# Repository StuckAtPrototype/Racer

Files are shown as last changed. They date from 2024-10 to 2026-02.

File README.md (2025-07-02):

# Micro Racer Car - StuckAtPrototype

*thank you for the overwhelmingly positve support!! such an inspiration to keep making fun open source content!*

## New Youtube video about improvements 
Lots of new improvements and I am now selling a kit for these! Check out the video here:
https://www.youtube.com/watch?v=FulhEs5R5WU
My Kickstarter failed, so I open sourced it (https://www.youtube.com/watch?v=FulhEs5R5WU)

## Original Youtube Video
A bit of a back-story of how this project came to be. 

My Kickstarter failed, so I open sourced it (https://www.youtube.com/watch?v=6jzG-BMannc)

Sub if you like what you see.

*Some pictures of the project*

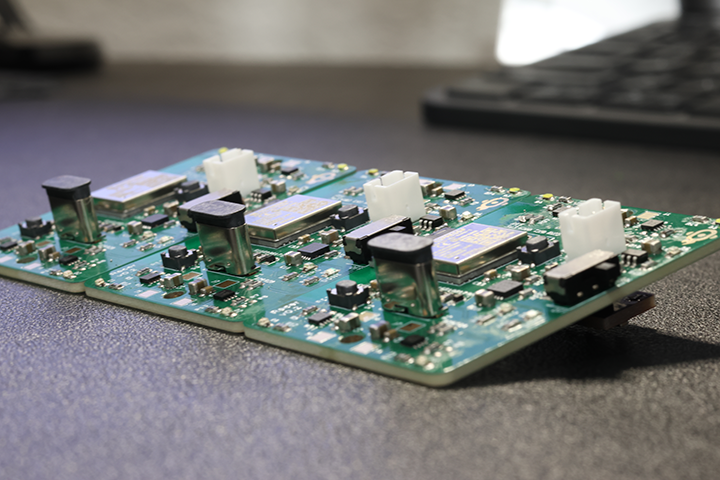
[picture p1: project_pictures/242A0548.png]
Picture of PCB car


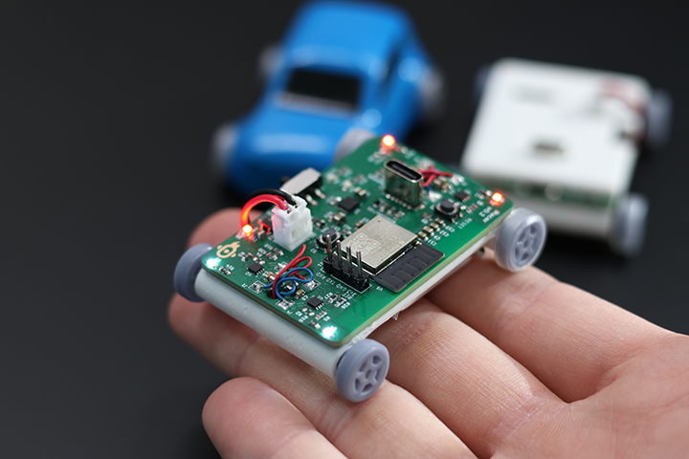
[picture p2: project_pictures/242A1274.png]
Picture of PCB car


## Hardware Remote for this car

https://github.com/StuckAtPrototype/Thumbtroller

## Project Structure
The project consists of
1. Firmware
2. Hardware
3. Mechanical 
4. Scripts

These are structured into their own files. I could have used submodules, but decided against it.  

### 1. Firmware
Code for the little car. This lives on the ESP32

#### Requirements
- ESP32 IDF version 5.3.1
- USB to Serial dongle
- Target set to ESP32-H2

### 2. Hardware

#### Schematic
PDF schematic included for your viewing pleasure. 
#### PCBs
All the gerber files you'd need to send to a fab house. 
#### Kicad
All the files you'd need to expand and work on this further. If you'd like. 

### 3. Mechanical

#### Enclosure
All the step files you need to make one of these. Extrusion printer works well for this part.  

#### Wheels
A bit of caution on this one.. you'll need an SLA printer. 

### 4. Scripts
Did anyone say neural networks? 

This folder has all the python code you'd need to train up your own neural network for the car. It also consists scripts that let you drive it using a keyboard -- just in case you dont want to make a physical controller.  

#### Requirements
- Python 3
- You'll need to install a bunch of pip modules 

#### Training the neural network
Training the neural network is as simple as running the training script with the data in the `color_data.txt` file. For data format see the sample data in the file. You need to stick to the formatting. 

To train run `python trainer.py`

#### Keyboard controller
To run the script `python controller.py`

Use `w` `s` `a` `d` for control. Modify the script for different speeds, etc

*Protocol for motor control* 

60,1,60,1,5 -- translates to:

motor side A: speed 60, direction forward

motor side B: speed 60, direction forward

500 miliseconds run time

See firmware file `motor.c` if you need more details

## What the project could use
1. Cleanup, but thats true for almost anything out there
2. Some fun code that makes the little car drive using the color sensor -- think very fancy line follower
3. LLM integration -- ChatGPT driving a physical little robot? anyone? :)

## If you take it further
Let me know if you ever make one of these, I'd love to see it. Seriously, that'd be exciting and inspiring to keep making my projects open source!

---
## License
### Apache 2.0 -- i.e. use as you'd like
http://www.apache.org/licenses/LICENSE-2.0

--- 
## Special Thanks
Thanks to Michael Angerer for his open sourced `esp32_ble_ota` project. I used it to get BLE running in this project. His blog post and github repo are a great resource. Check it out. https://github.com/michael-angerer/esp32_ble_ota

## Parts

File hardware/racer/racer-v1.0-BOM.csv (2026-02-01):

Designator | Quantity | Manufacturer Part Number | Package/Footprint | Description
U9 | 1 | TPS631000DRLR | TPS631000DRLR_TEX | TPS631000DRLR
R6,R26,R28,R29,R9,R1,R27,R11,R4 | 9 | WR06X103 JTL | R_0603_1608Metric | 10K
C2,C16,C20,C18,C5,C6,C19,C1,C22 | 9 | GRM188R61A106ME69D | C_0603_1608Metric | 10uF
S2 | 1 | RKB2SJK250SMTR LFS | SWITCH_0SMTRLFS | SWITCH_0SMTRLFS
C7,C12,C13,C24,C15,C3,C8,C14,C4,C23,C11,C25 | 12 | CC0603KRX7R7BB104 | C_0603_1608Metric | 0.1uF
R2 | 1 | RQ73C1J806RBTDF | R_0603_1608Metric | 806
U6 | 1 | AP2205-33W5-7 | AP2204 | AP2205
R23 | 1 | RT0603BRE071K43L | R_0603_1608Metric | 1.43K
J9 | 1 | GRPB032VWQS-RC | PinHeader_2x03_P1.27mm_Vertical_SMD | Conn_02x03_SMT
Q1 | 1 | BSS138 | SOT-23 | BSS138
D9 | 1 | 150060RS75000 | C_0603_1608Metric | LED_RED
R17,R22,R18 | 3 | RC0603FR-075K1L | R_0603_1608Metric | 5K1
LED1,LED3,LED5,LED4,LED2 | 5 | IN-PI15TAT5R5G5B | IN-PI15_INL | IN-PI15TAT5R5G5B
D8 | 1 | 150060GS75000 | C_0603_1608Metric | LED_GREEN
U4,U1,U2,U3 | 4 | A3908EEETR-T | A3908 | A3908
J12 | 1 | B2B-PH-K-S | JST_PH_B2B-PH-K_1x02_P2.00mm_Vertical | JST 2.0 BATT
P1 | 1 | USB4105-GF-A | GCT_USB4105-GF-A | USB_C_Plug_USB2.0
TH1 | 1 | NTCG163JF103HT1 | R_0603_1608Metric | TH 10K
U5 | 1 | ESP32-H2-MINI-1 | MODULE_ESP32-H2-MINI-1-H2 | ESP32-H2-MINI-1
R3 | 1 | CR0603-FX-91R0ELF | R_0603_1608Metric | 91
R5 | 1 | ESR03EZPF4700 | R_0603_1608Metric | 470
L1 | 1 | CIGT252010EH1R0MNE | RES_CIGT252010 | 1uH
C10 | 1 | CC0603KRX5R8BB105 | C_0603_1608Metric | 1uF
R21,R20 | 2 | RC0603JR-07330RL | R_0603_1608Metric | 330
D5 | 1 | TPD1E10B06DYAR | D_SOD-523 | TPD1E10B06
S1 | 1 | JS102011SAQN | SW_JS102011SAQN | JS102011SAQN
R24 | 1 | ERJ-PB3B7502V | R_0603_1608Metric | 75K
U7 | 1 | MCP73833T-AMI/MF | SON50P300X300X100-11N | MCP73833
C17 | 1 | GRM188R60J226MEA0J | C_0603_1608Metric | 22uF
R16 | 1 | RMCF0603FT1M00 | R_0603_1608Metric | 1M
C9 | 1 | GRM188C80E476ME05D | C_0603_1608Metric | 47uF
C21 | 1 | CL10A225KO8NNNC | C_0603_1608Metric | 2.2uF

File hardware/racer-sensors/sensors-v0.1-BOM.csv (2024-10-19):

Id | Designator | Footprint | Quantity | Designation | Supplier and ref | Notes
1 | R4,R5,R6,R3 | R_0603_1608Metric | 4 | 10K | WR06X103 JTL
2 | D1,D2 | LED_0603_1608Metric | 2 | LED | IN-S63AT5UW
3 | R2,R1 | R_0603_1608Metric | 2 | R | ESR03EZPF4700 | Note: I used a 470ohm resistor, but this might need to be adjusted to vary brightness
4 | C3 | C_0603_1608Metric | 1 | 4.7uF | GRM188R61A106ME69D | Replaced with 10uF
5 | C1,C2 | C_0603_1608Metric | 2 | 0.1uF | CC0603KRX7R7BB104
6 | U2 | SOT-23_TO-236_TDK | 1 | HAL1501SU-A | HAL1501SU-A
7 | U1 | FCSOT8_DTS_TEX | 1 | OPT4060DTSR | OPT4060DTSR
8 | J1 | PinHeader_2x03_P1.27mm_Vertical_SMD | 1 | Conn_02x03_SMT | 20021321-00006C4LF

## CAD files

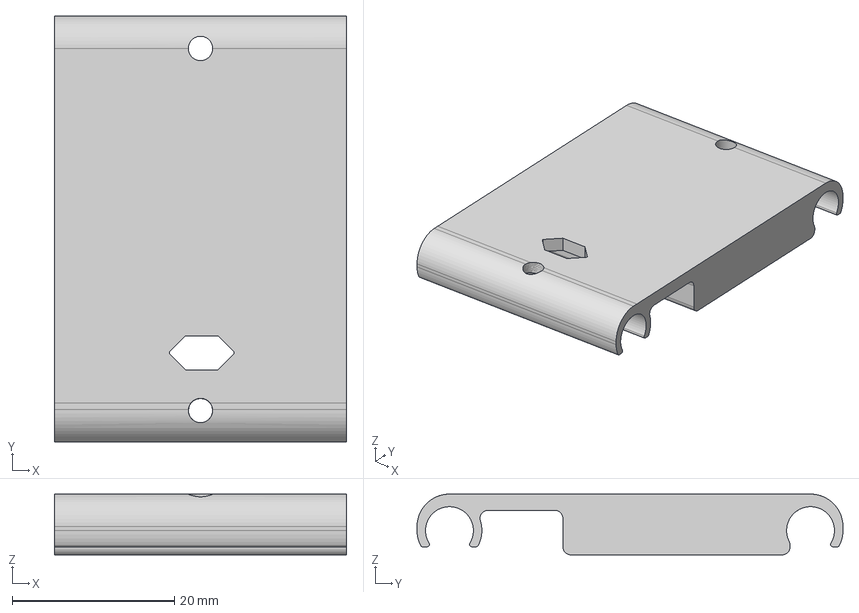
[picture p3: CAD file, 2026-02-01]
mechanical/main-enclosure-v1.0.step
36.0 x 52.5 x 7.50 mm

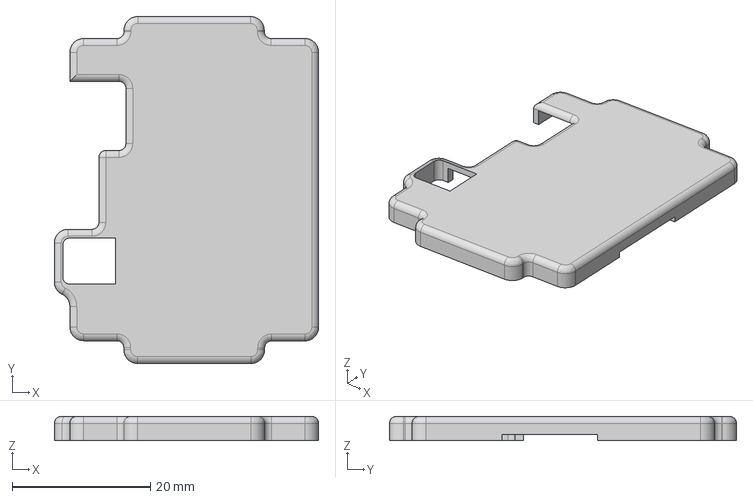
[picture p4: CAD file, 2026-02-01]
mechanical/top-enclosure-v1.0.step
38.2 x 50.2 x 3.50 mm

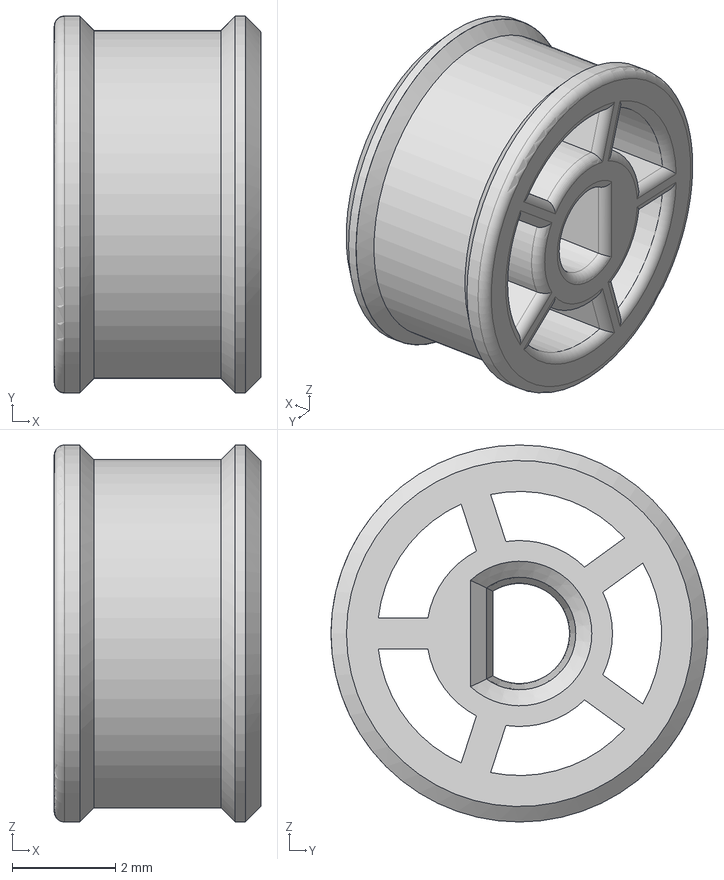
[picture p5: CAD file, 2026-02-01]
mechanical/wheel-v1.0.step
4.00 x 7.30 x 7.30 mm

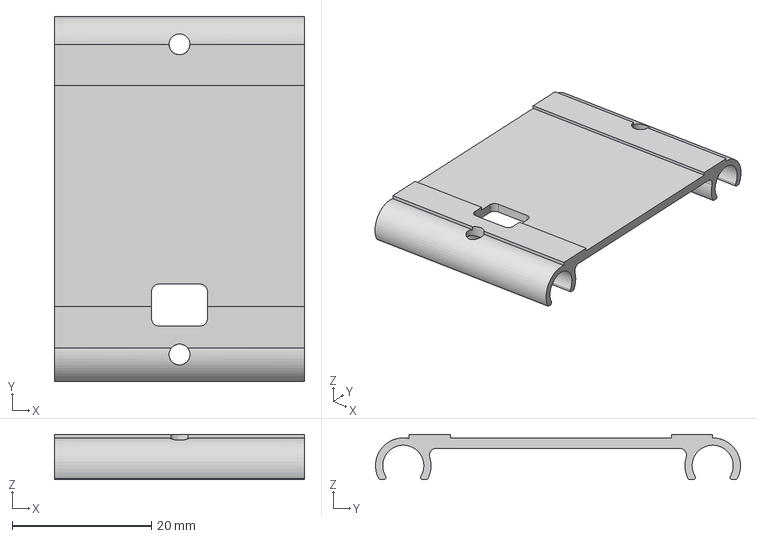
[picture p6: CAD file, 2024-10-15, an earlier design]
mechanical/previous versions/main-enclosure.step
36.0 x 52.5 x 6.50 mm

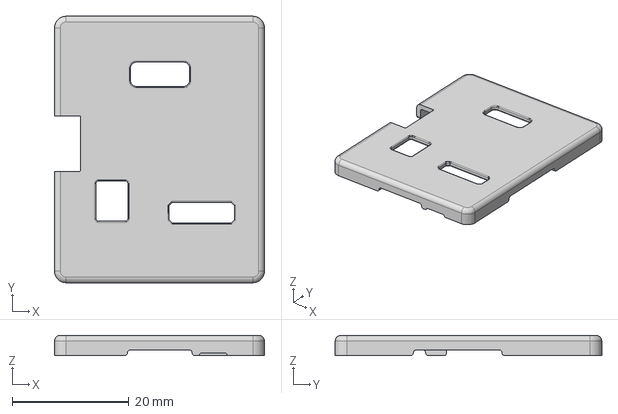
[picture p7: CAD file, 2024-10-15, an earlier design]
mechanical/previous versions/top-enclosure.step
36.0 x 45.7 x 3.50 mm

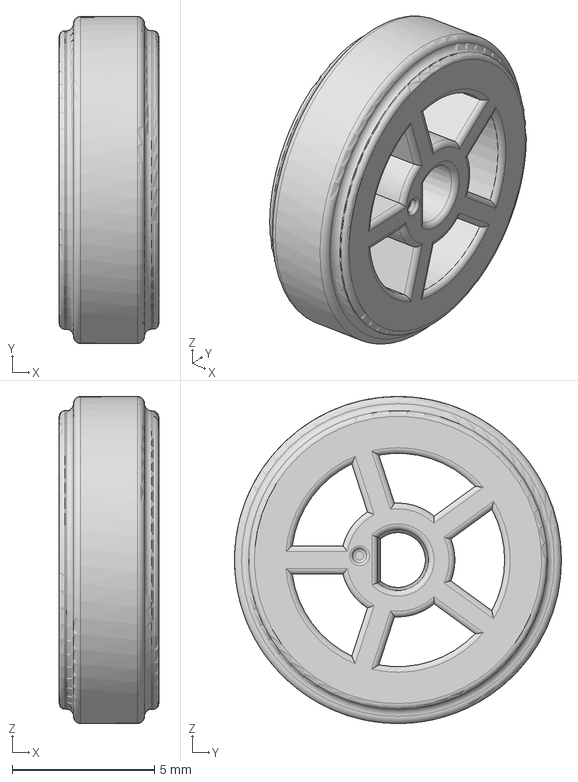
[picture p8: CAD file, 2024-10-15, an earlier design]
mechanical/previous versions/wheel.step
3.50 x 11.5 x 11.5 mm

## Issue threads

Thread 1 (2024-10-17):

PLZ Add PDF for Schematic and PCB artwork

puviarasud, 2024-10-17:
Hi good project. Please add a PDF copy of the schematic and PCB artwork for people to have a look at your design. not all have the tools installed . Thanks

oscarpeters, 2024-10-17:
Been working on improving readability of the schematics.
[RACER-v0.2.1.pdf](https://github.com/user-attachments/files/17410684/RACER-v0.2.1.pdf)

puviarasud, 2024-10-18:
Thanks , put it in the respective Github folder. I will look into it and suggest improvements, All the best.

StuckAtPrototype, 2024-10-19:
> Been working on improving readability of the schematics. [RACER-v0.2.1.pdf](https://github.com/user-attachments/files/17410684/RACER-v0.2.1.pdf)

if you want to open up a pull request I am happy to merge it in :)

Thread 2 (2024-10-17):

More obvious link to a video

gbraad, 2024-10-17:
Make the image in the `README.md` a screenshot with a play button. That makes it more obvious this is a link to the YouTube video. People do not read headings ;-)

StuckAtPrototype, 2024-10-18:
awesome! thank you! this is a brilliant idea! Ill do that

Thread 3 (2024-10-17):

Suggestion:  Add FPV capability via using esp32 cam.

villimikko, 2024-10-17:
Great project! Look really fun!

I think possibly adding FPV would make it perfect ( not sure if controller range is a limit)
Here is example project that is showing it is possible.

https://github.com/RomanLut/hx-esp32-cam-fpv

StuckAtPrototype, 2024-10-18:
neat! this would be fun for sure. I fly FPV freestyle quads and love FPV in general. I might make some youtube shorts showcasing the car with a chepo tiny whoop camera on it :)

AirborneEagle, 2024-10-18:
I would certainly be there for that!
To I used to be quite deep into the fpv drone racing world.
I've also built custom fpv RC cars for a small business that I started once.
Thank you for sharing this awesome project!

StuckAtPrototype, 2024-10-19:
I have analog FPV cameras, I used to be deep into freestyle FPV. I even designed my own frames! I still love my frame more than any other out there, sadly not much time to fly these days. I might do a completely from scratch hardware and firmware as a project one day. I know there is a ton of open source stuff, but I have some fun twists in mind :)

That said, I might do a short running around the house with an FPV camera on one of these!

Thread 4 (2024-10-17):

Please add BOMs

alexspurling, 2024-10-17:
It would be helpful to include BOM files for the PCB (including the motors) so we know which parts to order (same goes for the controller project).

tobiasoort, 2024-10-17:
(this way more novice users can use a service like JLCPCB to order the completed PCB and get going quickly too)

Rubines, 2024-10-17:
Thank you for sharing this fun project!
Please add the motor data, do you have a link where I could source them ?

mianzhi, 2024-10-17:
> Thank you for sharing this fun project! Please add the motor data, do you have a link where I could source them ?

I guess they are "6 mm geared coreless motor, 1200 rpm nominal speed at 3V". @StuckAtPrototype thanks for sharing the project, please correct me if i was wrong.

StuckAtPrototype, 2024-10-17:
@mianzhi thats correct!

I will be sharing a BOM late tonight!

for now, you can find the motors by searching "6mm planetary motors 1200 rpm"

Rubines, 2024-10-17:
Thank you both for your help!
@mianzhi @StuckAtPrototype

StuckAtPrototype, 2024-10-18:
initial BOM added for the racer. I still have the sensor board and the controller to do, but that will have to wait until tomorrow 👍

hazerty565, 2024-10-18:
hi, I would like to know whats is motor it is use? have you got a reference? Thank you

StuckAtPrototype, 2024-10-19:
All BOMs are in! if there are any problems, lets open a new issue. closing this out 🎉

Closed 2024-10-19.

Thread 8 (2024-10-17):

Use USB Pins for programming

majuss, 2024-10-17:
Hi there,

thank you for sharing your project!  The H2-mini is a "C6 variant" which means it comes with onboard USB, no programmer etc. neccessary! Why didn't you connect the D- and D+ lines of the USB-C port to the MCU. That way you could easily program it via USB and could skip the UART header entirely.

StuckAtPrototype, 2024-10-19:
Hi! thats so true! I will do that for the next project. Thanks!! For this project, I would have to upgrade the connector as the one I used does only power. But this is a very good idea. Ill keep it in mind for the project I am working on now :) Closing this out for this one. thanks again!

andistorm, 2024-11-06:
Nice idea,

currently there is only a 6-pin USB-C connector used. If i am not wrong, you would need at least 8 pins, with `D-` and `D+`.

This would mean we need to change pcb, which we try not to do for `v0.2.0` release, but after checking at JLCPCB I realized this connector is currently not available, so maybe we need to change USB-C Connector anyways.

Since this issue is in discussion again, I reopen it.

What do you think @StuckAtPrototype

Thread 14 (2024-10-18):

CPL file

AirborneEagle, 2024-10-18:
I am totally new to the world of PCB making and assembly.
Do you have a cpl file that you could include?

StuckAtPrototype, 2024-10-18:
ill add it to the list, thats a good point!

TexGG, 2024-10-19:
I was gonna ask the same. The project look amasing, the CPL will hepl produce the circuit easier :)

mr-ukas, 2024-10-30:
I created a pick&place file from Kicad. First time in my life, so better double check : D
For getting a PCBA-manufacturer's quote, it should be good enough 👍

PCB top edited to match JLCPCB requirements to format.
[racer-top-pos.csv](https://github.com/user-attachments/files/17579037/racer-top-pos.csv)
[CPL_miniRacer_position_pickNplace_JLC_top.xlsx](https://github.com/user-attachments/files/17579038/CPL_miniRacer_position_pickNplace_JLC_top.xlsx)
[racer-bottom-pos.csv](https://github.com/user-attachments/files/17579039/racer-bottom-pos.csv)

mr-ukas, 2024-10-30:
all revision V0.2

mr-ukas, 2024-10-30:
`What do you mean by this? Is it not based on master branch?`
It's the master branch. I just wanted to add this information about the revision, in case somebody will update the revision in the future.

`where you explain the steps you have done 👀`

I just re-named the columns according to this guide here:
https://jlcpcb.com/help/article/pick-place-file-for-pcb-assembly

andistorm, 2024-10-30:
>I just re-named the columns according to this guide here

Oh wow, you typed in all the rows by hand? I would have thought there is some tooling to  achieve this.

Did you have a look at [this guide](https://jlcpcb.com/help/article/How-to-generate-the-BOM-and-Centroid-file-from-KiCAD)?

mr-ukas, 2024-10-30:
> Did you have a look at [this guide](https://jlcpcb.com/help/article/How-to-generate-the-BOM-and-Centroid-file-from-KiCAD)?

yes, true, this page was my starting point.
I used also the MS excel to import the CSV-file to a regular excel sheet. This transferred the rows to proper columns, which had to be re-named ✌️

mr-ukas, 2024-10-30:
Feel free to creat a pull request to merge the files. I have no idea how this is done. It's late here :D

andistorm, 2024-10-30:
> Feel free to creat a pull request to merge the files.

Probably I will, but I want to try to generate this files by myself for this

fschrempf, 2024-11-07:
I'm usually using [Aisler](https://aisler.net/) to order PCBs (and optionally parts/assembly). They allow to upload the KiCad PCB file and get all the required data from it. For matching the components automatically it requires a ["MPN" field](https://community.aisler.net/t/documenting-parts/56) to be set as the "Manufacturer Part Number". I don't know the requirements for JLCPCB, but it would be great if we could also add the MPN field.

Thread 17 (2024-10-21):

Circuit boards

smebberson, 2024-10-21:
Are there only services that will allow me to have one the PCB printed with all of the electrical components in place? Are all of the files available for this project that would be needed for such a service?

I have no idea about how to make the final circuit board with everything soldered in place, but I would like to try and build this project.

I'm a software guy with some ESP32 programming experience

StuckAtPrototype, 2024-10-21:
Everything necessary is within the repo, that said, I will generate placement files which will make it much easier. I am happy that you want to build it! I would love to see it once you are done :) Also, feel free to open a thread in the discussions if you need any help! thanks for the support

Closed 2024-10-21.

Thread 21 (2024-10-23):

request for the charging circuit design and details used in the project

nithinmathewjoji, 2024-10-23:
# Request for LiPo Charger Circuit Design details

Dear **Mr. StuckAtPrototype**,

Kindly provide the circuit schematic, explaining:
   - The connections between components.
   - The placement of safety components like diodes and fuses.
   - Input/output terminals and how they interface with the battery.

blubbsy, 2024-10-23:
Hi,

is there a reason why to use a GPT text for asking this? But to answer your question: For the project simply the Microchip MCP73833 is used and in the datasheet you find this picture with values:

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

nithinmathewjoji, 2024-10-24:
Naa I'm just too lazy to type the whole thing dude 😆 🤣

DeepCoreSystem, 2024-10-24:
Open the KiCad project and you'll find the schematic

StuckAtPrototype, 2024-11-03:
everything needed is in the files. closing this out

Closed 2024-11-03.

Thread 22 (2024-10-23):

Question on Racer outside shell

aushe02, 2024-10-23:
I was looking at the mechanical step files and noticed there isn't a file for the outside shell of the Racer that goes over the enclosure, like in the picture below. I was wondering if you 3D printed that part. If you did, could you upload the file?

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

StuckAtPrototype, 2024-10-25:
The original body does not fit the new version and at this point id have to dig deep to find the original body files. But, yes it was printed on an SLA printer

Closed 2024-10-25.

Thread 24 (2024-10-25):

Bom for thumbtroller is missing

Mk-arc, 2024-10-25:
I couldnt find the bom for the controller. Could you also add it?

FrerichsJacob, 2024-10-29:
It's in the Thumbtroller repository!
https://github.com/StuckAtPrototype/Thumbtroller/tree/master/hardware

StuckAtPrototype, 2024-10-30:
closing this out. its here https://github.com/StuckAtPrototype/Thumbtroller/blob/master/hardware/controller-v0.2-BOM.csv

Closed 2024-10-30.

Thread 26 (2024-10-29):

sdkconfig missing

paolosanchi, 2024-10-29:
Hello, I'm trying to compile and run the firmware on an esp32 wroom devkit, I currently don't have a esp mini 1, but I guess it should be compatible.
I could compile it by changing the default configuration (I basically had to activate the BLE).
The file sdkconfig is missing and I'm afraid I miss some kind of configurations.
The firmware runs but it seems to get stuck.
this is the output:

```
I (31) boot: ESP-IDF v5.3.1 2nd stage bootloader
I (31) boot: compile time Oct 29 2024 05:32:28
I (31) boot: Multicore bootloader
I (35) boot: chip revision: v3.0
I (39) boot.esp32: SPI Speed      : 40MHz
I (44) boot.esp32: SPI Mode       : DIO
I (48) boot.esp32: SPI Flash Size : 2MB
I (53) boot: Enabling RNG early entropy source...
I (58) boot: Partition Table:
I (62) boot: ## Label            Usage          Type ST Offset   Length
I (69) boot:  0 nvs              WiFi data        01 02 00009000 00006000
I (77) boot:  1 phy_init         RF data          01 01 0000f000 00001000
I (84) boot:  2 factory          factory app      00 00 00010000 00100000
I (92) boot: End of partition table
I (96) esp_image: segment 0: paddr=00010020 vaddr=3f400020 size=1a2f8h (107256) map
I (141) esp_image: segment 1: paddr=0002a320 vaddr=3ff80000 size=00004h (     4) load
I (141) esp_image: segment 2: paddr=0002a32c vaddr=3ffbdb60 size=04dech ( 19948) load
I (154) esp_image: segment 3: paddr=0002f120 vaddr=40080000 size=00ef8h (  3832) load
I (157) esp_image: segment 4: paddr=00030020 vaddr=400d0020 size=595c0h (366016) map
I (289) esp_image: segment 5: paddr=000895e8 vaddr=40080ef8 size=18570h ( 99696) load
I (341) boot: Loaded app from partition at offset 0x10000
I (341) boot: Disabling RNG early entropy source...
I (353) cpu_start: Multicore app
I (362) cpu_start: Pro cpu start user code
I (362) cpu_start: cpu freq: 160000000 Hz
I (362) app_init: Application information:
I (365) app_init: Project name:     hello_world
I (370) app_init: App version:      1807a4c-dirty
I (375) app_init: Compile time:     Oct 29 2024 12:30:22
I (381) app_init: ELF file SHA256:  8ac5c9a1f...
I (387) app_init: ESP-IDF:          v5.3.1
I (391) efuse_init: Min chip rev:     v0.0
I (396) efuse_init: Max chip rev:     v3.99
I (401) efuse_init: Chip rev:         v3.0
I (406) heap_init: Initializing. RAM available for dynamic allocation:
I (413) heap_init: At 3FFAFF10 len 000000F0 (0 KiB): DRAM
I (419) heap_init: At 3FFB6388 len 00001C78 (7 KiB): DRAM
I (425) heap_init: At 3FFB9A20 len 00004108 (16 KiB): DRAM
I (431) heap_init: At 3FFC5CC8 len 0001A338 (104 KiB): DRAM
I (438) heap_init: At 3FFE0440 len 00003AE0 (14 KiB): D/IRAM
I (444) heap_init: At 3FFE4350 len 0001BCB0 (111 KiB): D/IRAM
I (450) heap_init: At 40099468 len 00006B98 (26 KiB): IRAM
I (458) spi_flash: detected chip: winbond
I (461) spi_flash: flash io: dio
W (465) spi_flash: Detected size(4096k) larger than the size in the binary image header(2048k). Using the size in the binary image header.
W (479) i2c: This driver is an old driver, please migrate your application code to adapt `driver/i2c_master.h`
I (490) coexist: coex firmware version: 4482466
I (495) main_task: Started on CPU0
I (505) main_task: Calling app_main()
I (505) gpio: GPIO[27]| InputEn: 0| OutputEn: 1| OpenDrain: 0| Pullup: 0| Pulldown: 0| Intr:0
I (505) gpio: GPIO[26]| InputEn: 0| OutputEn: 1| OpenDrain: 0| Pullup: 0| Pulldown: 0| Intr:0
I (515) gpio: GPIO[25]| InputEn: 0| OutputEn: 1| OpenDrain: 0| Pullup: 0| Pulldown: 0| Intr:0
I (525) gpio: GPIO[22]| InputEn: 0| OutputEn: 1| OpenDrain: 0| Pullup: 0| Pulldown: 0| Intr:0
LED flash period set to 10 ticks
LED 0 (GPIO 27) set to ON
LED 1 (GPIO 26) set to ON
LED 2 (GPIO 25) set to ON
LED 3 (GPIO 22) set to ON
LED 3 (GPIO 22) set to OFF
LED 2 (GPIO 25) set to OFF
LED 1 (GPIO 26) set to ON
LED 0 (GPIO 27) set to ON
I (565) BTDM_INIT: BT controller compile version [b022216]
I (565) BTDM_INIT: Bluetooth MAC: 40:22:d8:57:e3:b6
I (575) phy_init: phy_version 4830,54550f7,Jun 20 2024,14:22:08
I (895) gpio: GPIO[10]| InputEn: 1| OutputEn: 0| OpenDrain: 0| Pullup: 1| P
```
As you can see the last line is interrupted

StuckAtPrototype, 2024-10-30:
Hi, Ill add the sdkconfig, thats a good point. I never ran this firmware on anything but the esp32-h2, so not sure it would run. there could be a GPIO collision from what it looks like

paolosanchi, 2024-10-31:
Ok, I wait for the sdkconfig, meanwhile I'll get an esp-h2 devboard and try to build my own car.
I really love this project and I'd like to help in its development.
I've texted you in private in instagram, please check out your message requests.

StuckAtPrototype, 2024-11-03:
sdkconfig added

Closed 2024-11-03.

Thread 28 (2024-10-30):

Missing footprint for USB C Connector

andistorm, 2024-10-30:
## My Setup

kicad 8.0.6

## How To Reproduce

1. Checkout `master`branch
2. Open PCB
3. Update PCB from Schematic

## Error Log

```
Error: P1 pad A4 not found in kicad_reformed_custom_IC:CUI_UJC-VP-3-SMT-TR.
Error: P1 pad B4 not found in kicad_reformed_custom_IC:CUI_UJC-VP-3-SMT-TR.
Error: P1 pad A1 not found in kicad_reformed_custom_IC:CUI_UJC-VP-3-SMT-TR.
Error: P1 pad B1 not found in kicad_reformed_custom_IC:CUI_UJC-VP-3-SMT-TR.
Error: P1 pad A6 not found in kicad_reformed_custom_IC:CUI_UJC-VP-3-SMT-TR.
Error: P1 pad A7 not found in kicad_reformed_custom_IC:CUI_UJC-VP-3-SMT-TR.
```

## Explanation

Opening the schematic file show that `kicad_reformed_custom_IC:CUI_UJC-VP-3-SMT-TR` is used as the footprint.
The library `kicad_reformed_custom_IC` comes not with default kicad installation. I guess it was imported once, after choosing the USB C Connector.
The problem is one could only guess which USB C Connector should be used.

## Open Questions

1. Which USB C connector is used?
2. Should we add a custom footprint library to the project? (including this one)

StuckAtPrototype, 2024-11-03:
Thanks for raising the issue, I will create a separate repo with all my footprints, thats should help in the future as well. Connector is CUI_UJC-VP-3-SMT-TR

StuckAtPrototype, 2024-11-03:
added necessary libraries here https://github.com/StuckAtPrototype/StuckAtPrototypeKiCadLibs/tree/master

closing this out for now, though please let me know if it works after setting them up.

andistorm, 2024-11-06:
Unfortunately, that didn’t solve the problem, but I found out that the symbol and footprint didn’t match

See my PR: https://github.com/StuckAtPrototype/Racer/pull/33

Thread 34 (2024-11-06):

Make project ready for Release v0.2.0

andistorm, 2024-11-06:
Let's work on having a `v0.2.0` release.

The idea of this release is to keep the state of software/hardware as it is right now,
but to enable easier fabrication at for example JLCPCB

This issue sums up what is needed to do before releasing:

Bugfixes:
- [ ] https://github.com/StuckAtPrototype/Racer/issues/28 : To allow opening kicad project out of the box (without warnings)

Enhancements:
- [ ] https://github.com/StuckAtPrototype/Racer/issues/14
- [ ] Add documentation: How to remake

Process:
- [ ] Make test order at JLCPCB

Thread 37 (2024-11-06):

Use cheaper Motor Driver from Texas instruments

andistorm, 2024-11-06:
### Discussed in https://github.com/StuckAtPrototype/Racer/discussions/12

<div type='discussions-op-text'>

<sup>Originally posted by **nledevil** October 17, 2024</sup>
I am starting to add LCSC part numbers to the schematic so I can have jcbpcb create/populate the board. I noticed you are using Allegra A3908 brushed dc motor drivers. Is there a reason for this? A3908's are pretty pricey and a Texas Instruments motor driver would be significantly cheaper. Would there be any drawback to using a cheaper driver to make the overall cost per unit lower?</div>

andistorm, 2024-11-06:
If it is a drop-in-replacement we could think about adding this to [`v0.2.0` release](https://github.com/StuckAtPrototype/Racer/issues/34)

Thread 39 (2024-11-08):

Incorrect resistor part number in BOM

FrerichsJacob, 2024-11-08:
Racer and Thumbtroller BOMs list RMCF0603JT5R10 (5.1 ohm) where they should say RMCF0603JT5K10 (5.1k ohm)

StuckAtPrototype, 2024-11-12:
Agreed, thats a mistake in the part number. The entire BOM should be double checked

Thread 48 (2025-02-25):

Instructions to order parts

hdattada, 2025-02-25:
Hi I am a noob trying to figure out how to source all the parts to assemble this. Unfortunately, the documentation currently seems a bit overwhelming for me. I tried to order the enclosure off an online retailer using the step files. It requires the user to configure the material for each of the part. I am sorry if there are already instructions on how to do this. Could someone please help me out?

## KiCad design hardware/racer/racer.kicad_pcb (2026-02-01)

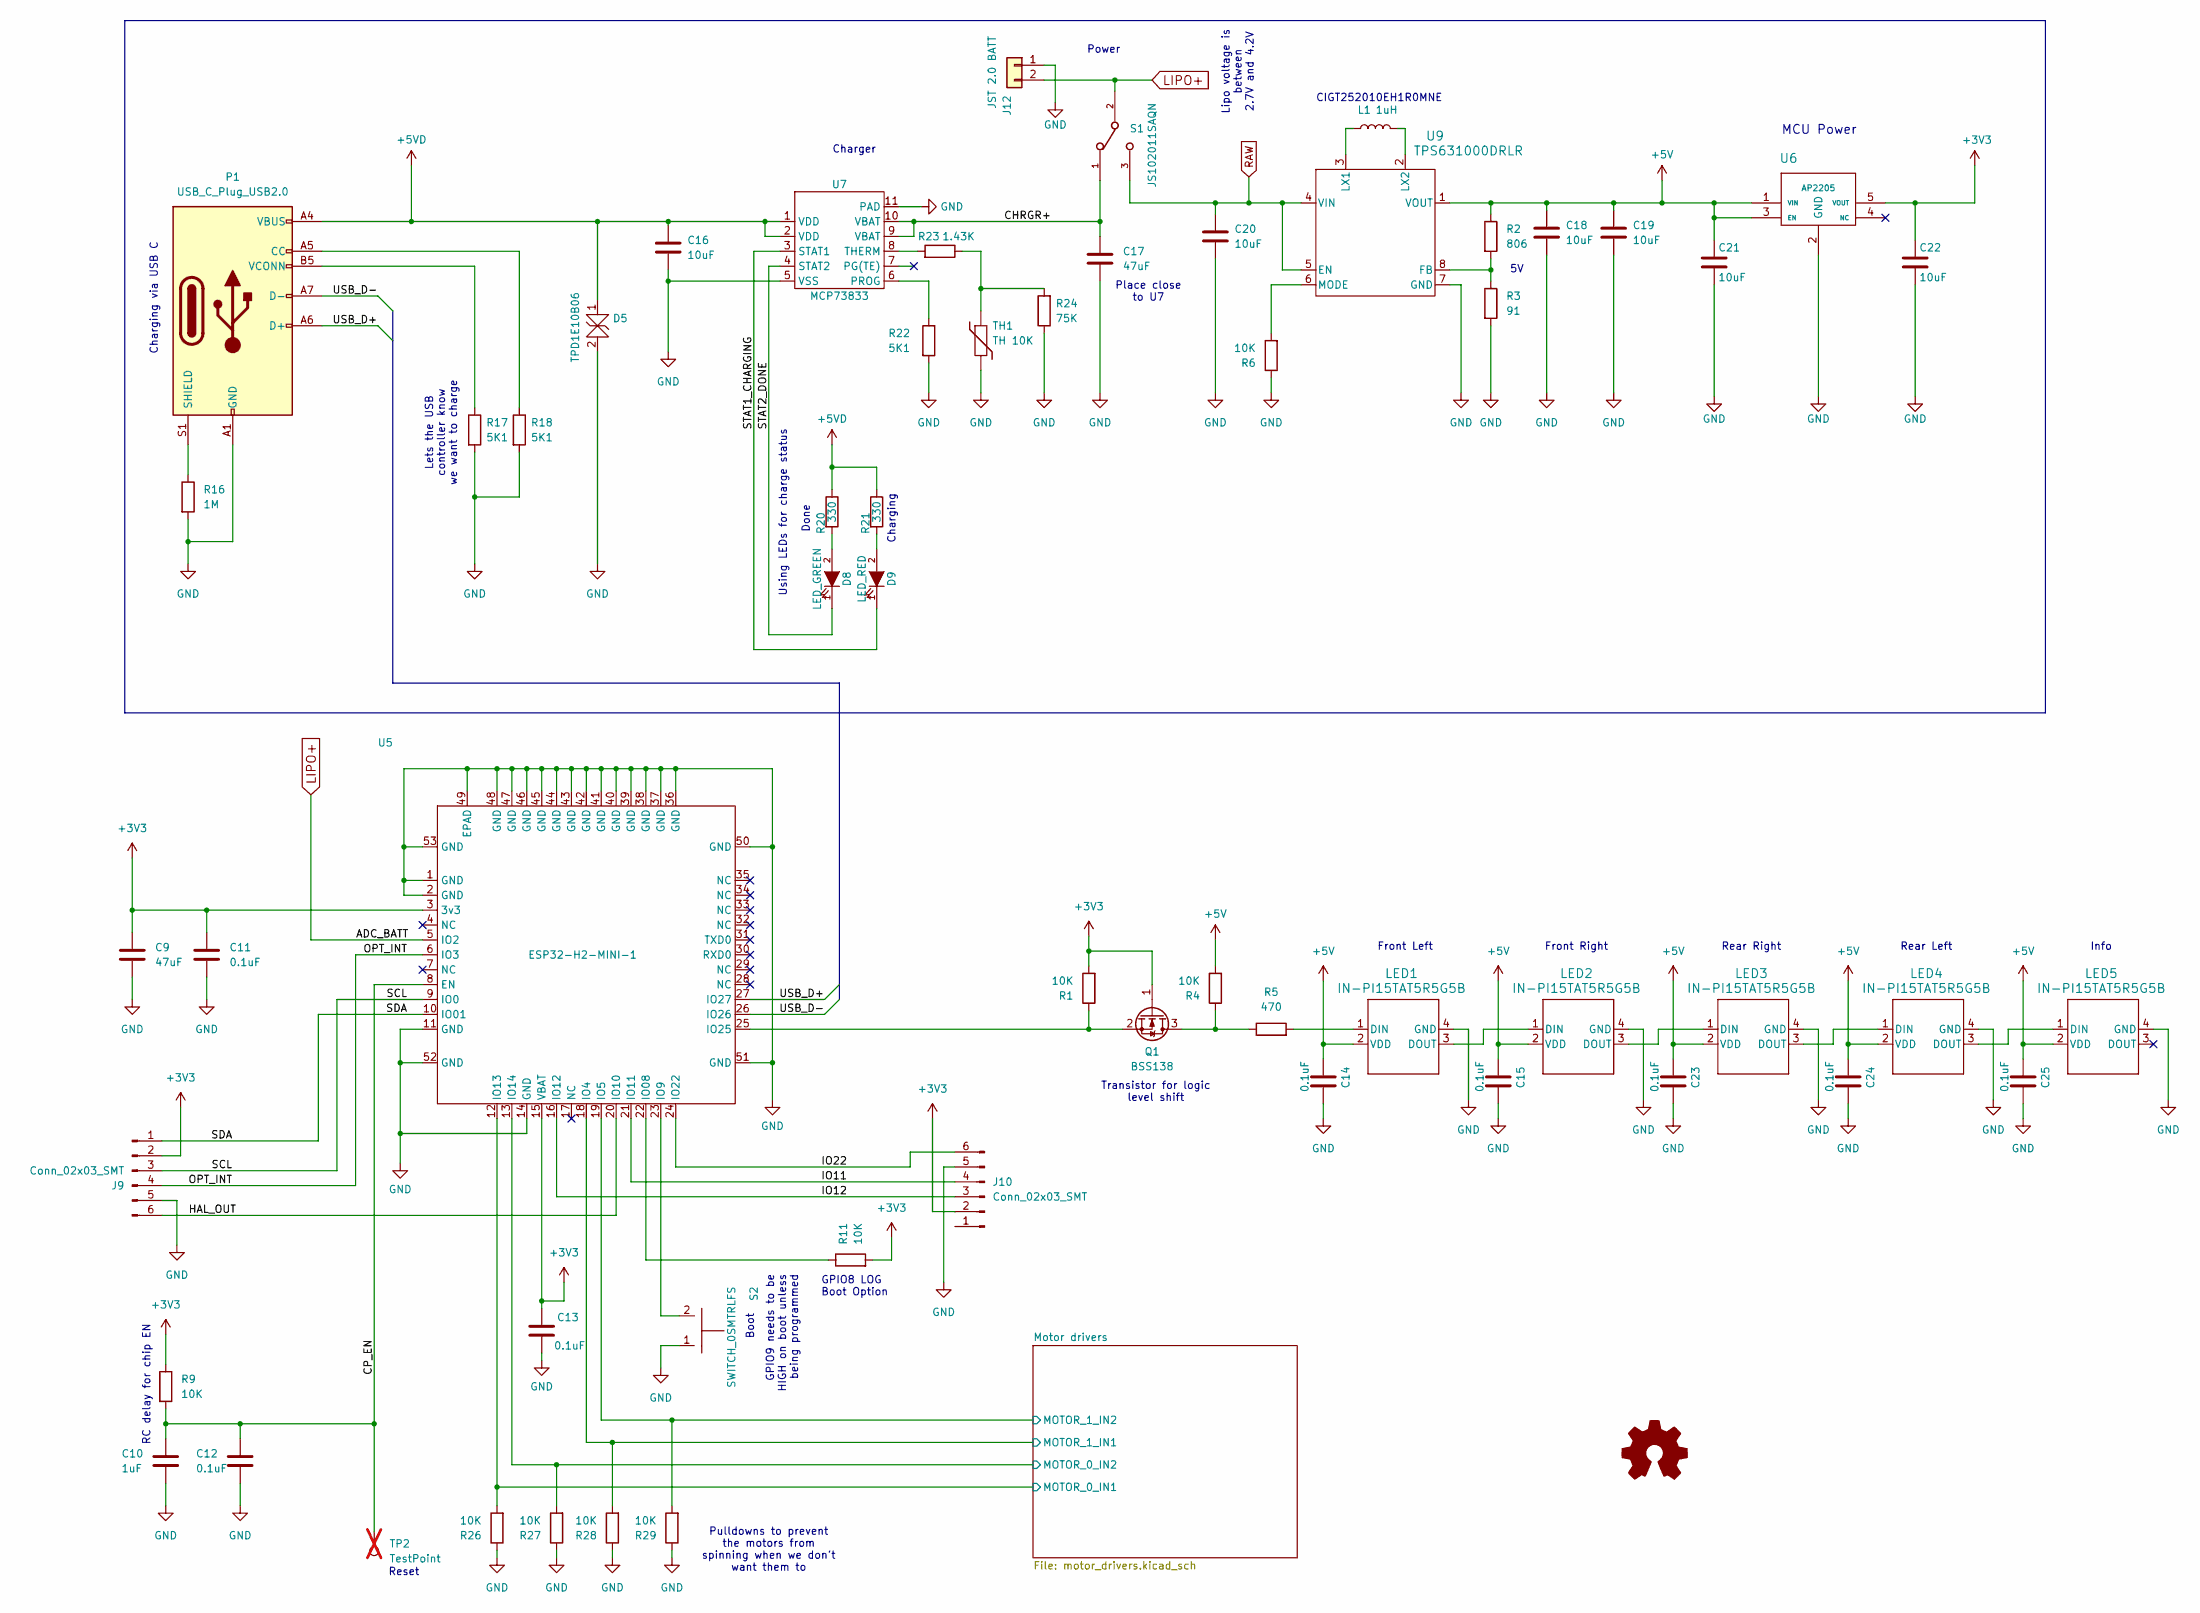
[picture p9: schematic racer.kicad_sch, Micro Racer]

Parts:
C9, C17: 47uF; C_0603_1608Metric
C10: 1uF; C_0603_1608Metric
C11, C12, C13, C14, C15, C23, C24, C25: 0.1uF; C_0603_1608Metric
C16, C18, C19, C20, C21, C22: 10uF; C_0603_1608Metric
D5: TPD1E10B06; D_SOD-523
D8: LED_GREEN; C_0603_1608Metric
D9: LED_RED; C_0603_1608Metric
J9, J10: Conn_02x03_SMT; PinHeader_2x03_P1.27mm_Vertical_SMD
J12: JST 2.0 BATT; JST_PH_B2B-PH-K_1x02_P2.00mm_Vertical
L1: 1uH; RES_CIGT252010
LED1, LED2, LED3, LED4, LED5: IN-PI15TAT5R5G5B; IN-PI15_INL
P1: USB_C_Plug_USB2.0; GCT_USB4105-GF-A
Q1: BSS138; SOT-23
R1, R4, R6, R9, R11, R26, R27, R28, R29: 10K; R_0603_1608Metric
R2: 806; R_0603_1608Metric
R3: 91; R_0603_1608Metric
R5: 470; R_0603_1608Metric
R16: 1M; R_0603_1608Metric
R17, R18, R22: 5K1; R_0603_1608Metric
R20, R21: 330; R_0603_1608Metric
R23: 1.43K; R_0603_1608Metric
R24: 75K; R_0603_1608Metric
S1: JS102011SAQN; SW_JS102011SAQN
S2: SWITCH_0SMTRLFS
TH1: TH 10K; R_0603_1608Metric
TP2: TestPoint; TestPoint_Pad_1.5x1.5mm; not fitted
U5: ESP32-H2-MINI-1; MODULE_ESP32-H2-MINI-1-H2
U6: AP2205; AP2204
U7: MCP73833; SON50P300X300X100-11N
U9: TPS631000DRLR; TPS631000DRLR_TEX

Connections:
+3V3: C9.1, C11.1, C13.1, C22.1, J9.2, J10.2, Q1.1 (G), R1.2, R9.1, R11.2, U5.3 (3v3), U5.15 (VBAT), U6.5 (VOUT)
+5V: C14.1, C15.1, C18.1, C19.1, C21.1, C23.1, C24.1, C25.1, LED1.2 (VDD), LED2.2 (VDD), LED3.2 (VDD), LED4.2 (VDD), LED5.2 (VDD), R2.1, R4.2, U6.1 (VIN), U6.3 (EN), U9.1 (VOUT)
+5VD: C16.1, D5.1, P1.A4 (VBUS), P1.A9 (VBUS), P1.B4 (VBUS), P1.B9 (VBUS), R20.1, R21.1, U7.1 (VDD), U7.2 (VDD)
/CHRGR+: C17.1, S1.1, U7.9 (VBAT), U7.10 (VBAT)
/CP_EN: C10.1, C12.1, R9.2, TP2.1, U5.8 (EN)
/HAL_OUT: J9.6, U5.20 (IO10)
/IO11: J10.4, U5.21 (IO11)
/IO12: J10.3, U5.16 (IO12)
/IO22: J10.6, U5.24 (IO22)
/OPT_INT: J9.4, U5.6 (IO3)
/SCL: J9.3, U5.9 (IO0)
/SDA: J9.1, U5.10 (IO01)
/STAT1_CHARGING: D9.1 (K), U7.3 (STAT1)
/STAT2_DONE: D8.1 (K), U7.4 (STAT2)
/USB_D+: P1.A6 (D+), U5.27 (IO27)
/USB_D-: P1.A7 (D-), U5.26 (IO26)
GND: C9.2, C10.2, C11.2, C12.2, C13.2, C14.2, C15.2, C16.2, C17.2, C18.2, C19.2, C20.2, C21.2, C22.2, C23.2, C24.2, C25.2, D5.2, J9.5, J10.5, J12.1, LED1.4 (GND), LED2.4 (GND), LED3.4 (GND), LED4.4 (GND), LED5.4 (GND), P1.A1 (GND), P1.A12 (GND), P1.B1 (GND), P1.B12 (GND), R3.2, R6.1, R16.2, R17.2, R18.2, R22.2, R24.1, R26.1, R27.1, R28.1, R29.1, S2.1, TH1.2, U5.1 (GND), U5.2 (GND), U5.11 (GND), U5.14 (GND), U5.36 (GND), U5.37 (GND), U5.38 (GND), U5.39 (GND), U5.40 (GND), U5.41 (GND), U5.42 (GND), U5.43 (GND), U5.44 (GND), U5.45 (GND), U5.46 (GND), U5.47 (GND), U5.48 (GND), U5.49 (EPAD), U5.50 (GND), U5.51 (GND), U5.52 (GND), U5.53 (GND), U6.2 (GND), U7.5 (VSS), U7.11 (PAD), U9.7 (GND); also elsewhere on the board
LIPO+: J12.2, S1.2, U5.5 (IO2)
MOTOR_0_IN1: R26.2, U5.12 (IO13); also elsewhere on the board
MOTOR_0_IN2: R27.2, U5.13 (IO14); also elsewhere on the board
MOTOR_1_IN1: R28.2, U5.18 (IO4); also elsewhere on the board
MOTOR_1_IN2: R29.2, U5.19 (IO5); also elsewhere on the board
unnamed: D8.2 (A), R20.2
unnamed: D9.2 (A), R21.2
unnamed: LED1.1 (DIN), R5.2
unnamed: LED1.3 (DOUT), LED2.1 (DIN)
unnamed: LED2.3 (DOUT), LED3.1 (DIN)
unnamed: LED3.3 (DOUT), LED4.1 (DIN)
unnamed: LED4.3 (DOUT), LED5.1 (DIN)
unnamed: P1.A5 (CC), R18.1
unnamed: P1.S1 (SHIELD), R16.1
unnamed: P1.B5 (VCONN), R17.1
unnamed: Q1.3 (D), R4.1, R5.1
unnamed: Q1.2 (S), R1.1, U5.25 (IO25)
unnamed: R23.1, R24.2, TH1.1
unnamed: R11.1, U5.22 (IO08)
unnamed: S2.2, U5.23 (IO9)
unnamed: R22.1, U7.6 (PROG)
unnamed: R23.2, U7.8 (THERM)
unnamed: R2.2, R3.1, U9.8 (FB)
unnamed: L1.1, U9.3 (LX1)
unnamed: L1.2, U9.2 (LX2)
unnamed: R6.2, U9.6 (MODE)
RAW: C20.1, S1.3, U9.4 (VIN), U9.5 (EN); also elsewhere on the board

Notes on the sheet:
Lipo voltage is between 2.7V and 4.2V
Charging via USB C
Using LEDs for charge status
RC delay for chip EN
Lets the USB controller know we want to charge
Front Right
Power
Rear Right
Reset
GPIO9 needs to be HIGH on boot unless being programmed
Pulldowns to prevent the motors from spinning when we don't want them to
Charger
GPIO8 LOG Boot Option
Charging
Done
Info
MCU Power
Front Left
CIGT252010EH1R0MNE
Rear Left
Place close to U7
Boot
Transistor for logic level shift

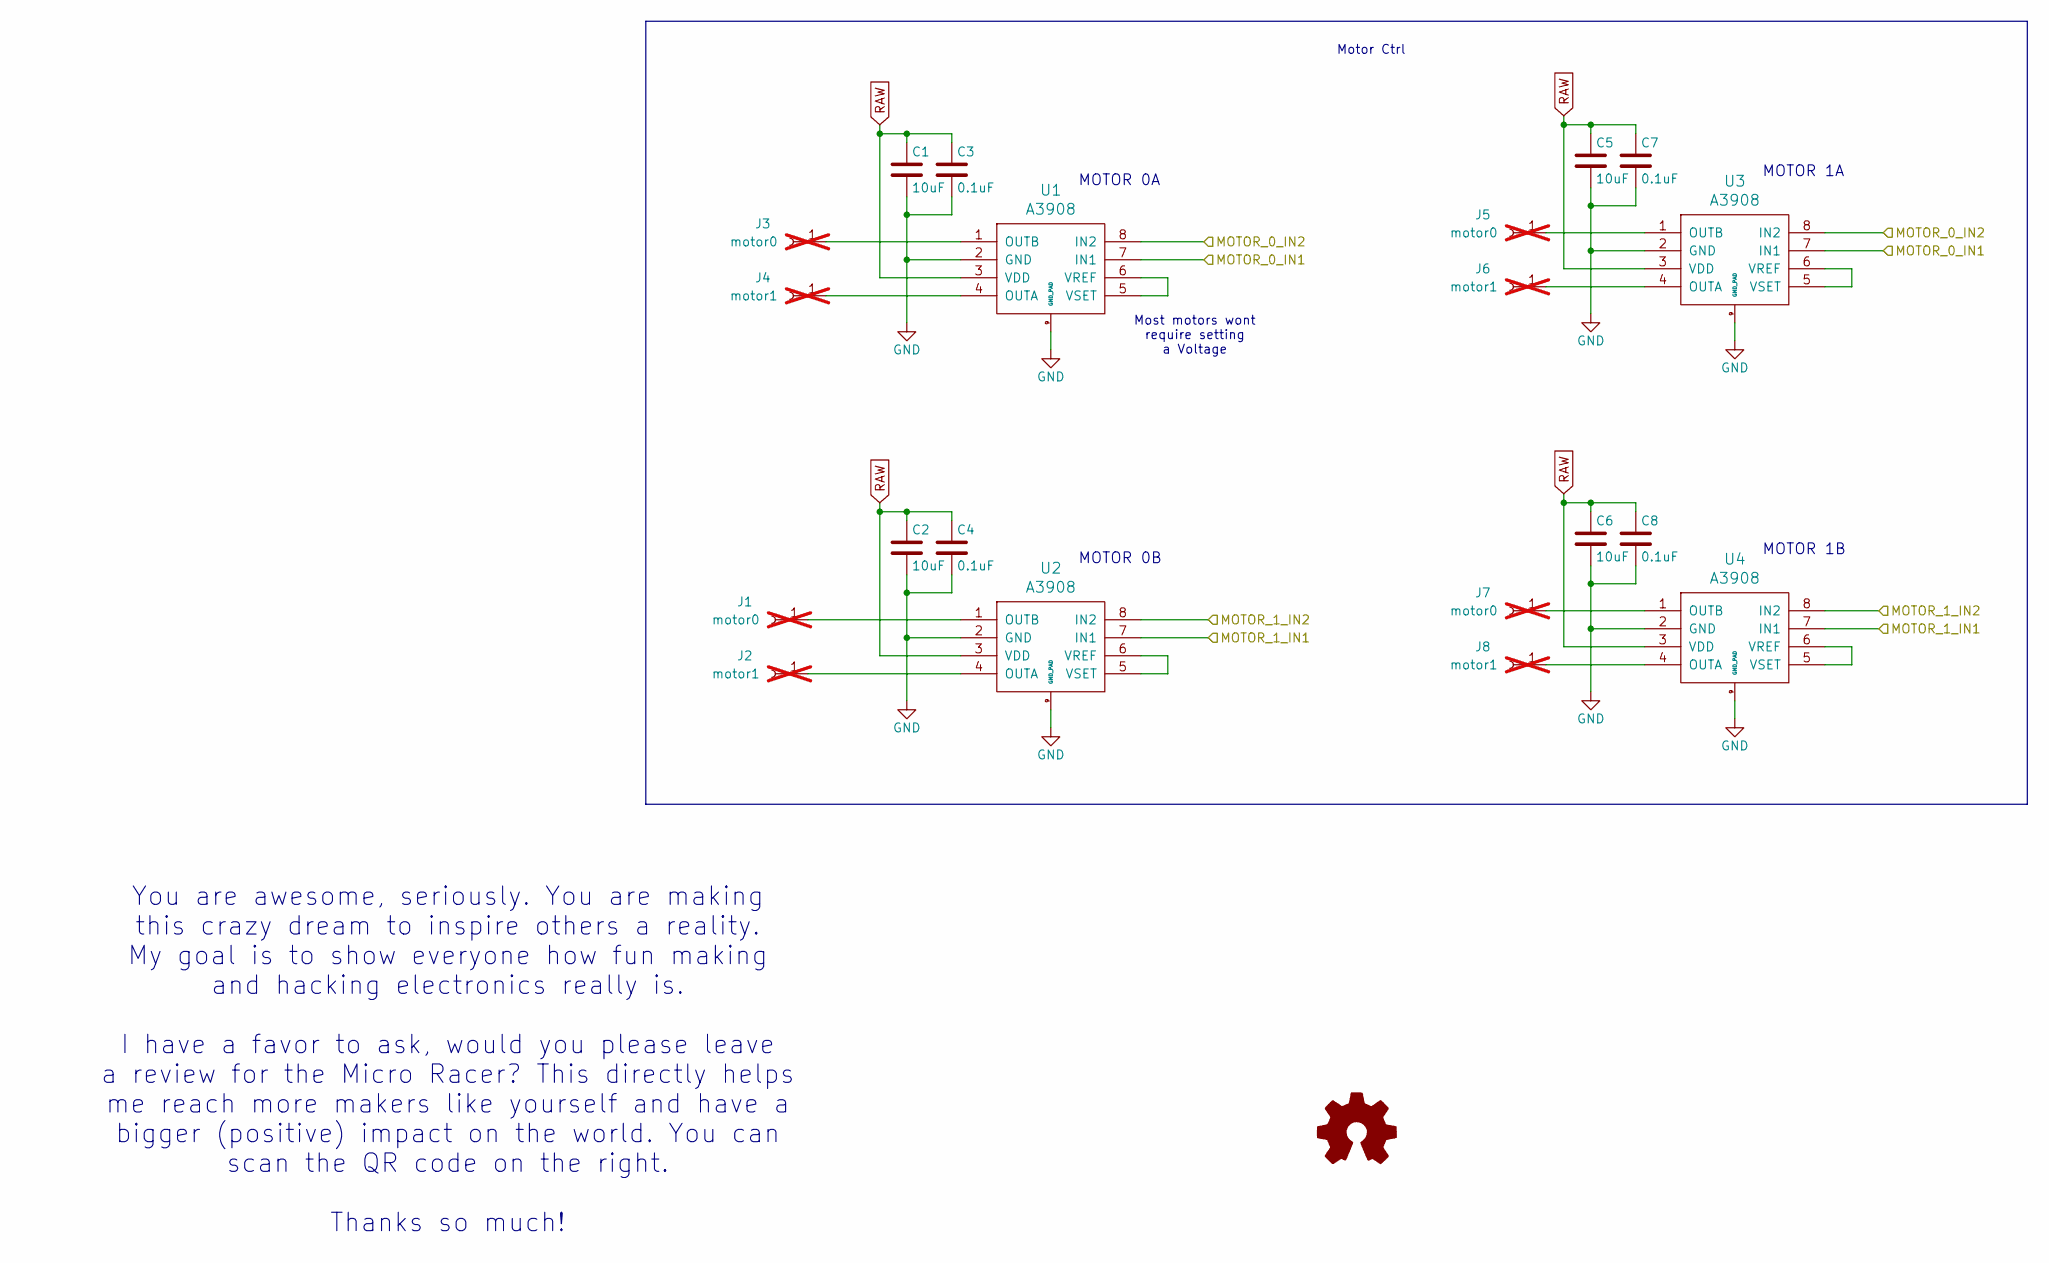
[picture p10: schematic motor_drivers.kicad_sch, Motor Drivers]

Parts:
C1, C2, C5, C6: 10uF; C_0603_1608Metric
C3, C4, C7, C8: 0.1uF; C_0603_1608Metric
J1, J3, J5, J7: motor0; TestPoint_Pad_2.0x2.0mm; not fitted
J2, J4, J6, J8: motor1; TestPoint_Pad_2.0x2.0mm; not fitted
U1, U2, U3, U4: A3908

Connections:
GND: C1.2, C2.2, C3.2, C4.2, C5.2, C6.2, C7.2, C8.2, U1.2 (GND), U1.9 (GND_PAD), U2.2 (GND), U2.9 (GND_PAD), U3.2 (GND), U3.9 (GND_PAD), U4.2 (GND), U4.9 (GND_PAD); also elsewhere on the board
MOTOR_0_IN1: U1.7 (IN1), U3.7 (IN1); also elsewhere on the board
MOTOR_0_IN2: U1.8 (IN2), U3.8 (IN2); also elsewhere on the board
MOTOR_1_IN1: U2.7 (IN1), U4.7 (IN1); also elsewhere on the board
MOTOR_1_IN2: U2.8 (IN2), U4.8 (IN2); also elsewhere on the board
unnamed: J1.1, U2.1 (OUTB)
unnamed: J2.1, U2.4 (OUTA)
unnamed: J3.1, U1.1 (OUTB)
unnamed: J4.1, U1.4 (OUTA)
unnamed: J5.1, U3.1 (OUTB)
unnamed: J6.1, U3.4 (OUTA)
unnamed: J7.1, U4.1 (OUTB)
unnamed: J8.1, U4.4 (OUTA)
unnamed: U1.5 (VSET), U1.6 (VREF)
unnamed: U2.5 (VSET), U2.6 (VREF)
unnamed: U3.5 (VSET), U3.6 (VREF)
unnamed: U4.5 (VSET), U4.6 (VREF)
RAW: C1.1, C2.1, C3.1, C4.1, C5.1, C6.1, C7.1, C8.1, U1.3 (VDD), U2.3 (VDD), U3.3 (VDD), U4.3 (VDD); also elsewhere on the board

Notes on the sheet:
Most motors wont require setting a Voltage
You are awesome, seriously. You are making this crazy dream to inspire others a reality. My goal is to show everyone how fun making and hacking electronics really is. I have a favor to ask, would you please leave a review for the Micro Racer? This directly helps me reach more makers like yourself a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
MOTOR 1B
MOTOR 0A
Motor Ctrl
MOTOR 1A
MOTOR 0B

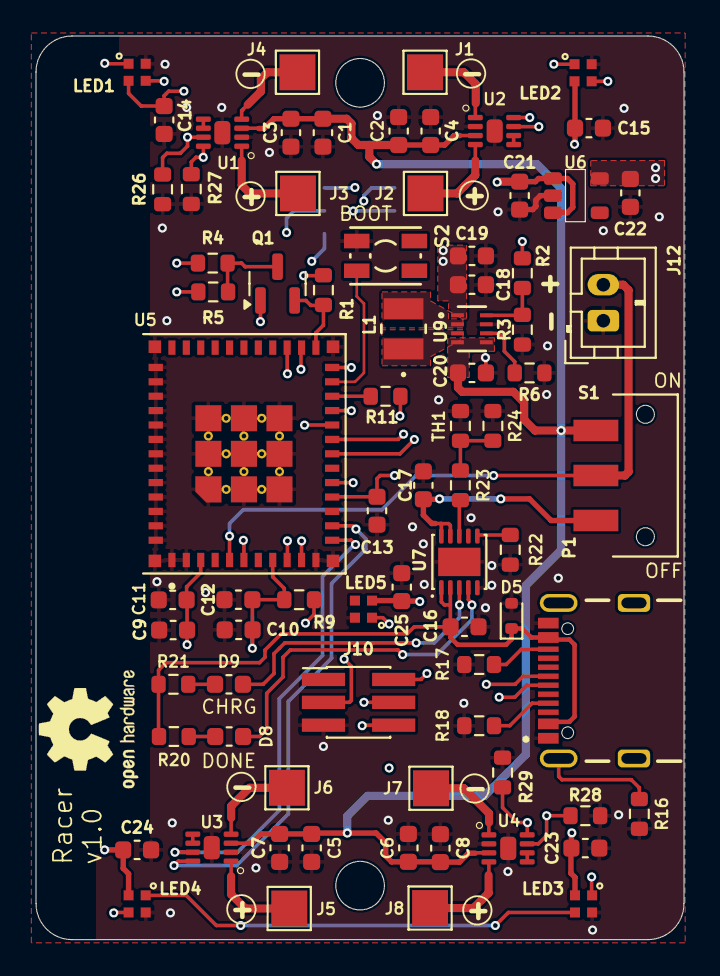
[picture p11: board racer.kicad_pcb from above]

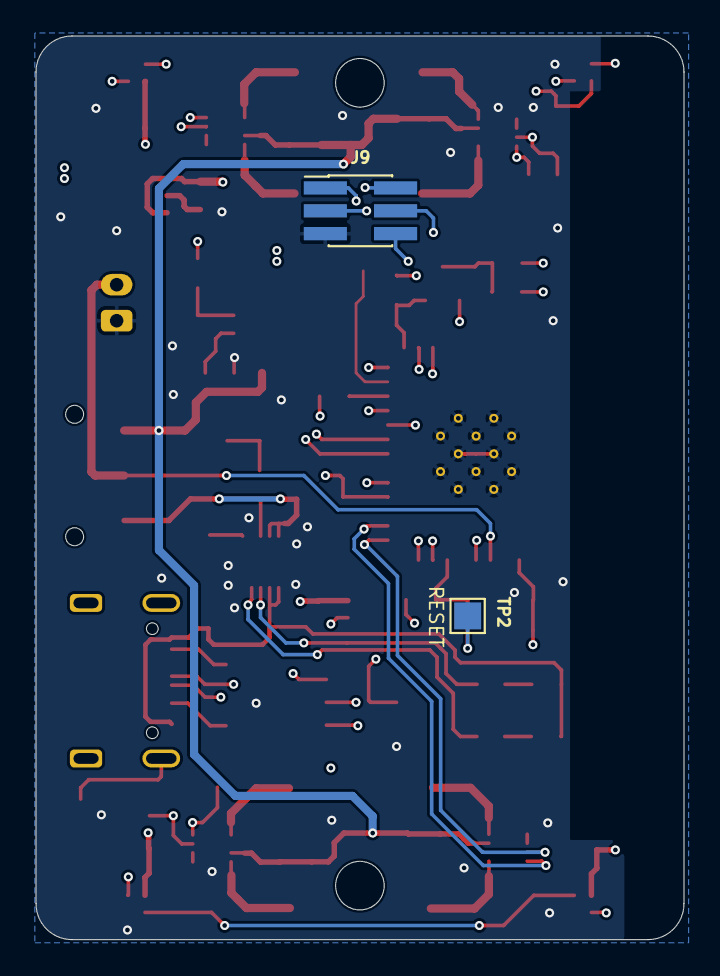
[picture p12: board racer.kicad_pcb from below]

Board: 4 copper layers, 36.0 x 50.2 mm, 79 parts (2 on the bottom side), 56 nets.

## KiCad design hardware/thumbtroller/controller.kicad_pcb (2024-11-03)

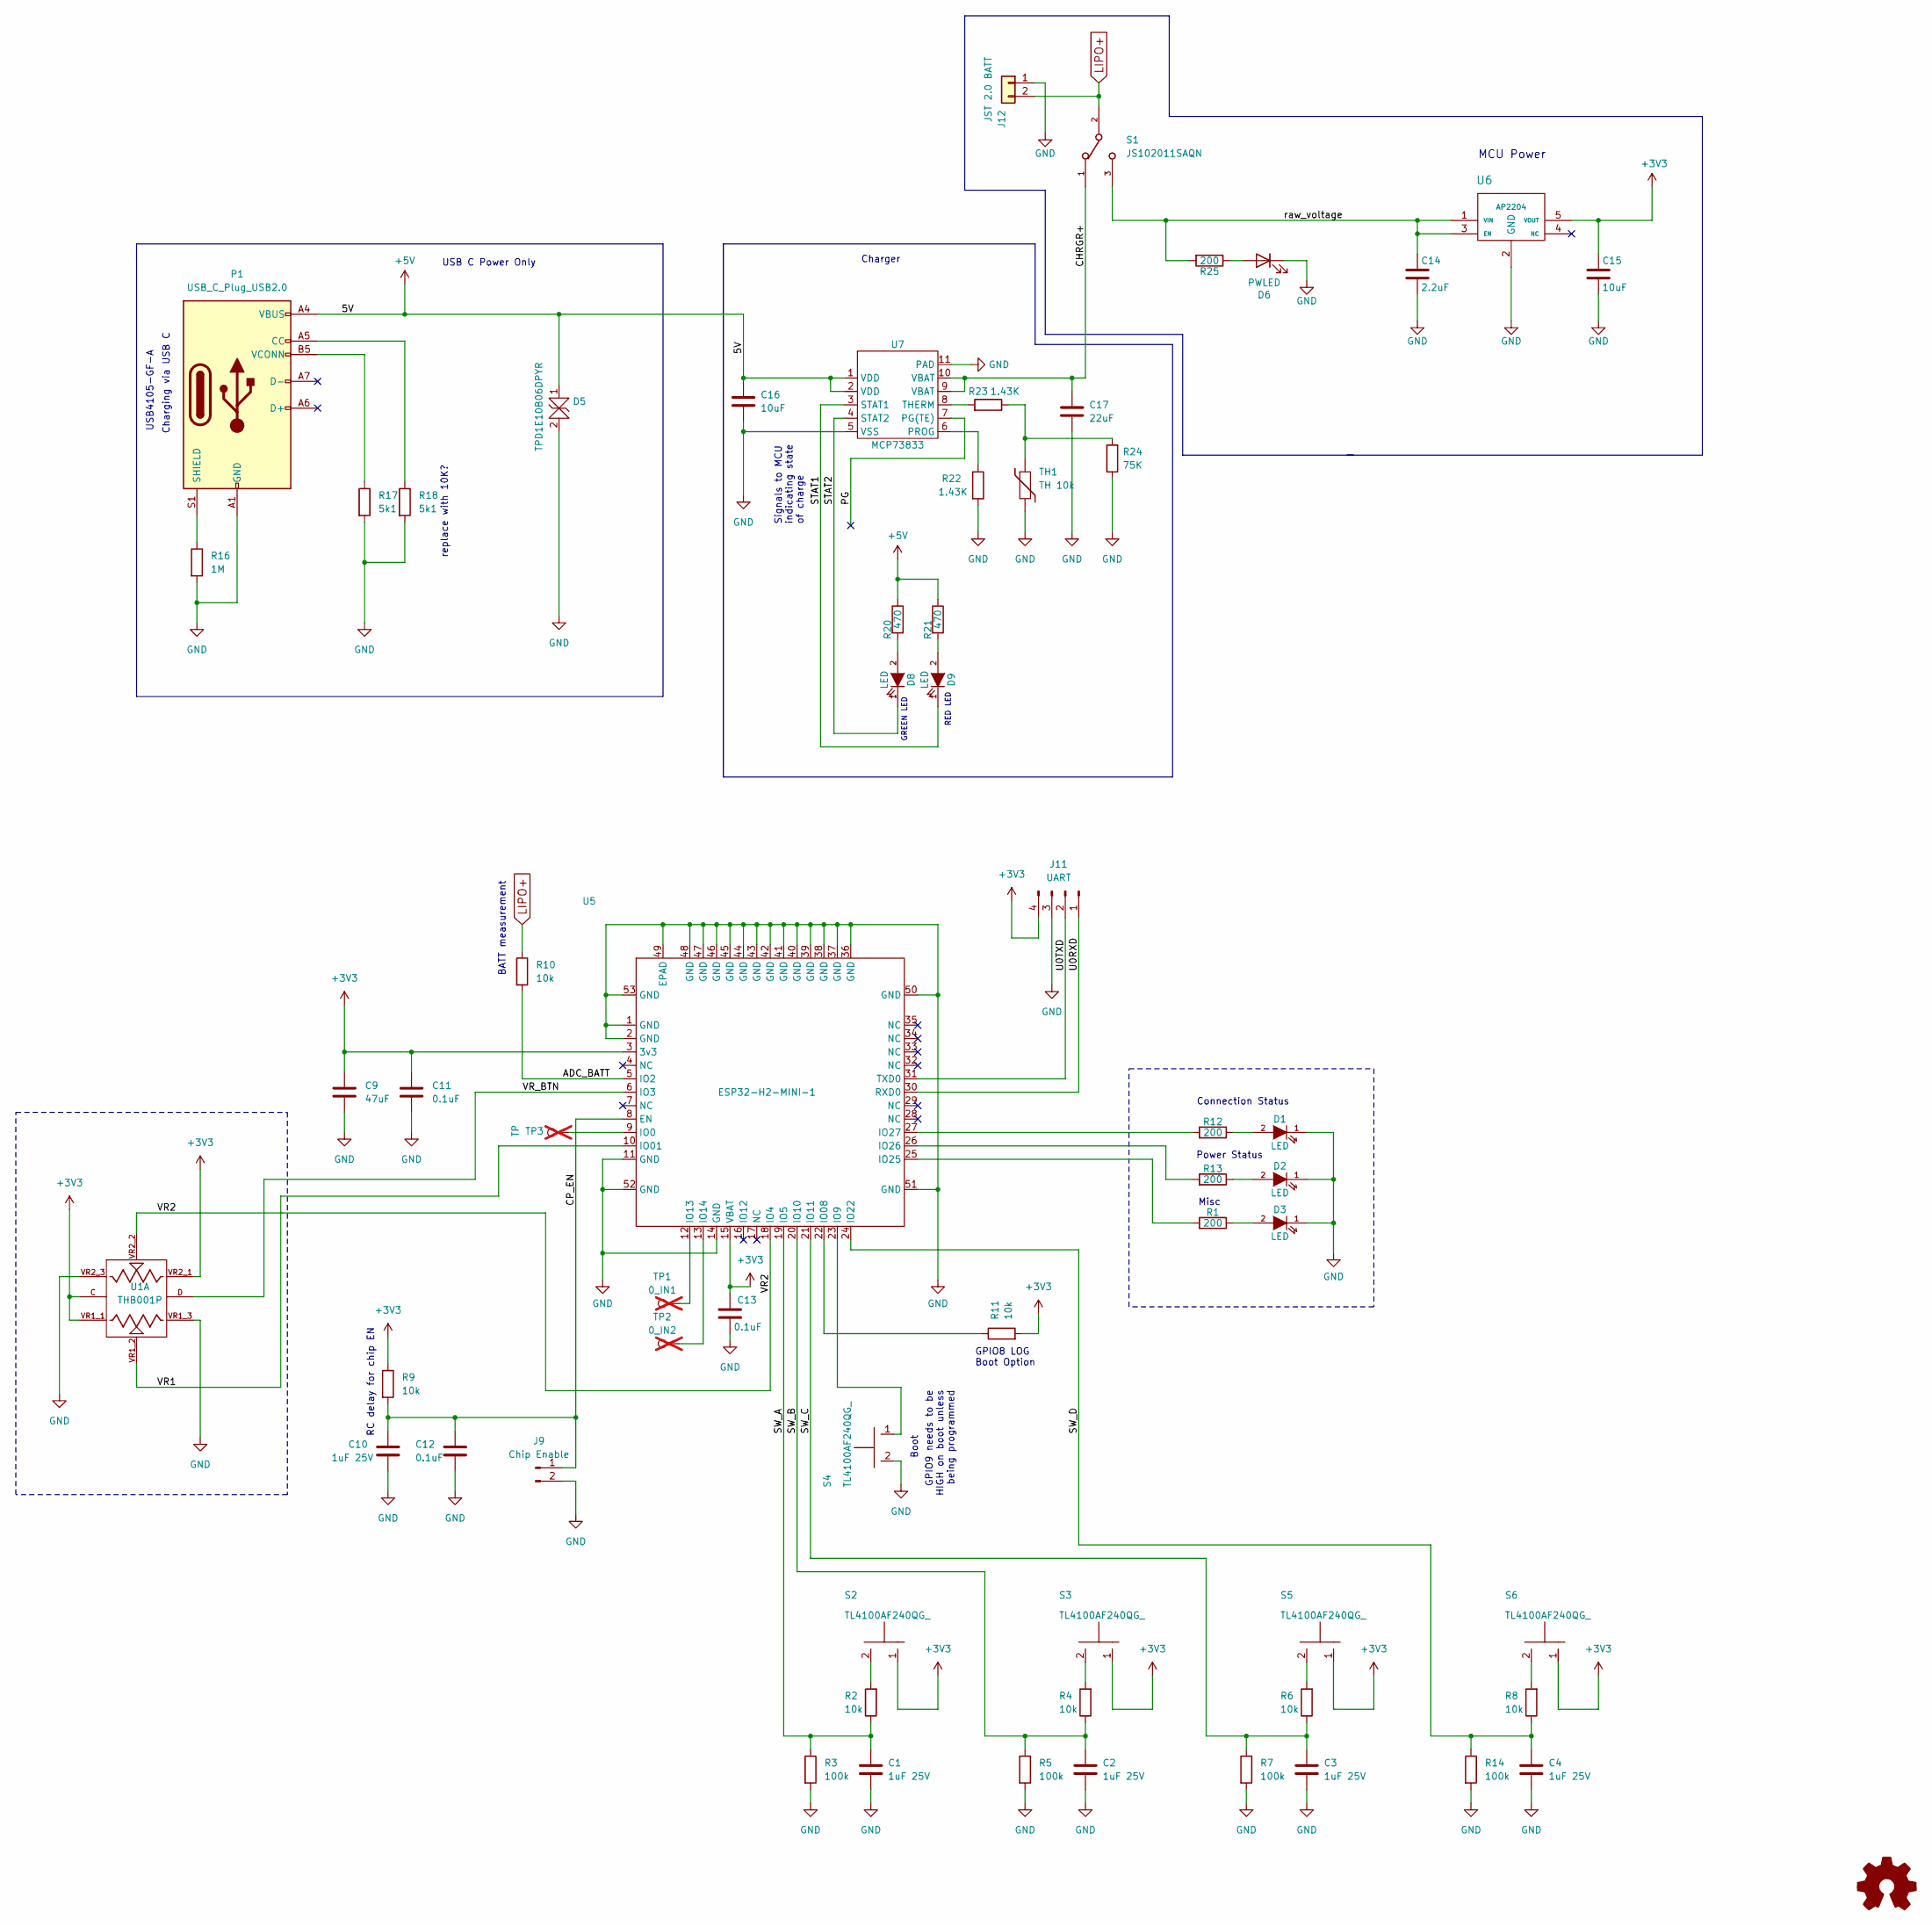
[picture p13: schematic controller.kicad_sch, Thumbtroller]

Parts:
C1, C2, C3, C4, C10: 1uF 25V; C_0603_1608Metric
C9: 47uF; C_0603_1608Metric
C11, C12, C13: 0.1uF; C_0603_1608Metric
C14: 2.2uF; C_0603_1608Metric
C15, C16: 10uF; C_0603_1608Metric
C17: 22uF; C_0603_1608Metric
D1, D2, D3, D8, D9: LED; C_0603_1608Metric
D5: TPD1E10B06DPYR; D_SOD-523
D6: PWLED; D_0603_1608Metric
J9: Chip Enable; PinHeader_1x02_P2.54mm_Vertical
J11: UART; PinHeader_1x04_P2.54mm_Vertical
J12: JST 2.0 BATT; JST_PH_B2B-PH-K_1x02_P2.00mm_Vertical
P1: USB_C_Plug_USB2.0; GCT_USB4105-GF-A
R1, R12, R13, R25: 200; R_0603_1608Metric
R2, R4, R6, R8, R9, R10, R11: 10k; R_0603_1608Metric
R3, R5, R7, R14: 100k; R_0603_1608Metric
R16: 1M; R_0603_1608Metric
R17, R18: 5k1; R_0603_1608Metric
R20, R21: 470; R_0603_1608Metric
R22, R23: 1.43K; R_0603_1608Metric
R24: 75K; R_0603_1608Metric
S1: JS102011SAQN; SW_JS102011SAQN
S2, S3, S4, S5, S6: TL4100AF240QG_; SW_PTS810_SJM_250_SMTR_LFS
TH1: TH 10k; R_0603_1608Metric
TP1: 0_IN1; TestPoint_Pad_1.0x1.0mm; not fitted
TP2: 0_IN2; TestPoint_Pad_1.0x1.0mm; not fitted
TP3: TP; TestPoint_Pad_D1.0mm; not fitted
U1: THB001P; CNK_THB001P; PARTREV 27 Jan 22
U5: ESP32-H2-MINI-1; MODULE_ESP32-H2-MINI-1-H2
U6: AP2204
U7: MCP73833; SON50P300X300X100-11N

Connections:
+3V3: C9.1, C11.1, C13.1, C15.1, J11.4, R9.1, R11.2, S2.1, S3.1, S5.1, S6.1, U1.C, U1.VR1_1, U1.VR2_1, U5.3 (3v3), U5.15 (VBAT), U6.5 (VOUT)
+5V: C16.1, D5.1, P1.A4 (VBUS), P1.A9 (VBUS), P1.B4 (VBUS), P1.B9 (VBUS), R20.1, R21.1, U7.1 (VDD), U7.2 (VDD)
/ADC_BATT: R10.2, U5.5 (IO2)
/CHRGR+: C17.1, S1.1, U7.9 (VBAT), U7.10 (VBAT)
/CP_EN: C10.1, C12.1, J9.1, R9.2, U5.8 (EN)
/PG: U7.7 (PG(TE))
/STAT1: D9.1 (K), U7.3 (STAT1)
/STAT2: D8.1 (K), U7.4 (STAT2)
/SW_A: C1.1, R2.1, R3.1, U5.19 (IO5)
/SW_B: C2.1, R4.1, R5.1, U5.20 (IO10)
/SW_C: C3.1, R6.1, R7.1, U5.21 (IO11)
/SW_D: C4.1, R8.1, R14.1, U5.24 (IO22)
/U0RXD: J11.1, U5.30 (RXD0)
/U0TXD: J11.2, U5.31 (TXD0)
/VR1: U1.VR1_2, U5.10 (IO01)
/VR2: U1.VR2_2, U5.18 (IO4)
/VR_BTN: U1.D, U5.6 (IO3)
/raw_voltage: C14.1, R25.2, S1.3, U6.1 (VIN), U6.3 (EN)
GND: C1.2, C2.2, C3.2, C4.2, C9.2, C10.2, C11.2, C12.2, C13.2, C14.2, C15.2, C16.2, C17.2, D1.1 (K), D2.1 (K), D3.1 (K), D5.2, D6.1 (K), J9.2, J11.3, J12.1, P1.A1 (GND), P1.A12 (GND), P1.B1 (GND), P1.B12 (GND), R3.2, R5.2, R7.2, R14.2, R16.2, R17.2, R18.2, R22.2, R24.1, S4.2, TH1.2, U1.VR1_3, U1.VR2_3, U5.1 (GND), U5.2 (GND), U5.11 (GND), U5.14 (GND), U5.36 (GND), U5.37 (GND), U5.38 (GND), U5.39 (GND), U5.40 (GND), U5.41 (GND), U5.42 (GND), U5.43 (GND), U5.44 (GND), U5.45 (GND), U5.46 (GND), U5.47 (GND), U5.48 (GND), U5.49 (EPAD), U5.50 (GND), U5.51 (GND), U5.52 (GND), U5.53 (GND), U6.2 (GND), U7.5 (VSS), U7.11 (PAD)
LIPO+: J12.2, R10.1, S1.2
unnamed: D1.2 (A), R12.1
unnamed: D2.2 (A), R13.1
unnamed: D3.2 (A), R1.1
unnamed: D6.2 (A), R25.1
unnamed: D8.2 (A), R20.2
unnamed: D9.2 (A), R21.2
unnamed: P1.A5 (CC), R18.1
unnamed: P1.S1 (SHIELD), R16.1
unnamed: P1.B5 (VCONN), R17.1
unnamed: R2.2, S2.2
unnamed: R4.2, S3.2
unnamed: R6.2, S5.2
unnamed: R8.2, S6.2
unnamed: R23.1, R24.2, TH1.1
unnamed: TP3.1, U5.9 (IO0)
unnamed: R11.1, U5.22 (IO08)
unnamed: S4.1, U5.23 (IO9)
unnamed: TP1.1, U5.12 (IO13)
unnamed: TP2.1, U5.13 (IO14)
unnamed: R1.2, U5.25 (IO25)
unnamed: R13.2, U5.26 (IO26)
unnamed: R12.2, U5.27 (IO27)
unnamed: R22.1, U7.6 (PROG)
unnamed: R23.2, U7.8 (THERM)

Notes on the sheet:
RED LED
BATT measurement
Charging via USB C
Signals to MCU indicating state of charge
RC delay for chip EN
replace with 10K?
Connection Status
GPIO8 LOG Boot Option
Boot
GPIO9 needs to be HIGH on boot unless being programmed
Charger
USB4105-GF-A
Power Status
MCU Power
GREEN LED
USB C Power Only
Misc

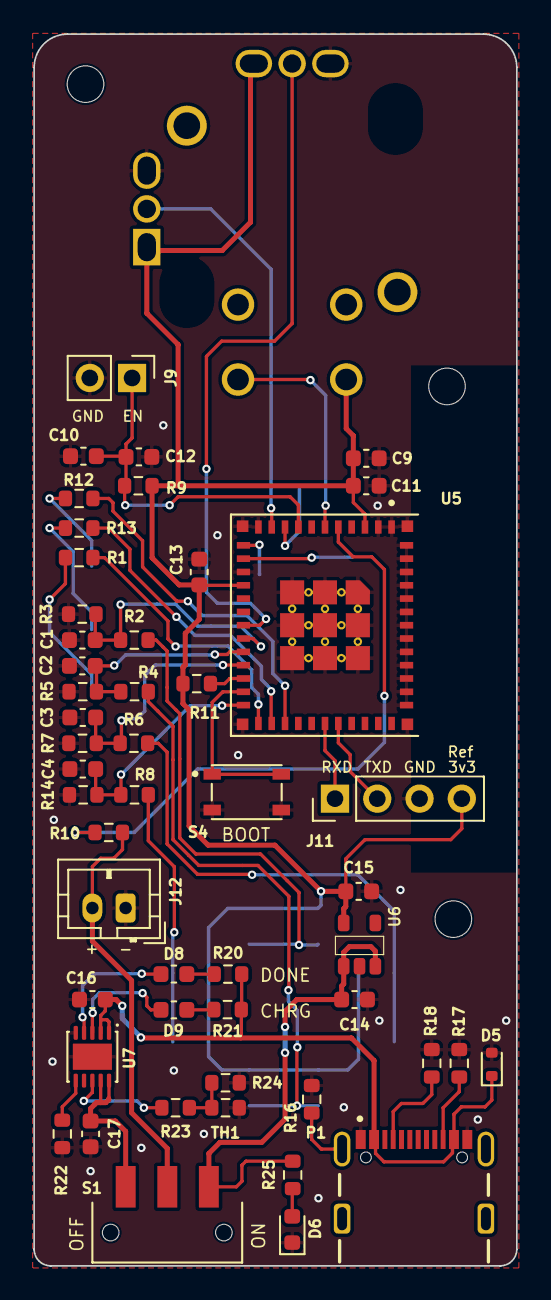
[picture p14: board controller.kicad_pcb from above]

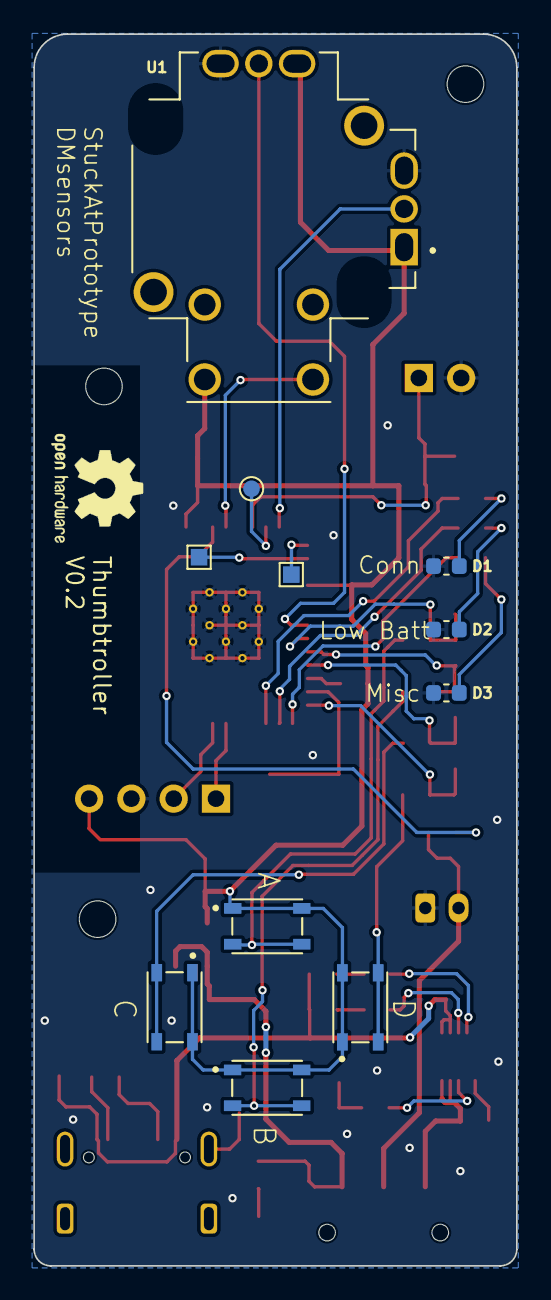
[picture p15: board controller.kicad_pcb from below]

Board: 4 copper layers, 29.0 x 74.0 mm, 61 parts (11 on the bottom side), 43 nets.

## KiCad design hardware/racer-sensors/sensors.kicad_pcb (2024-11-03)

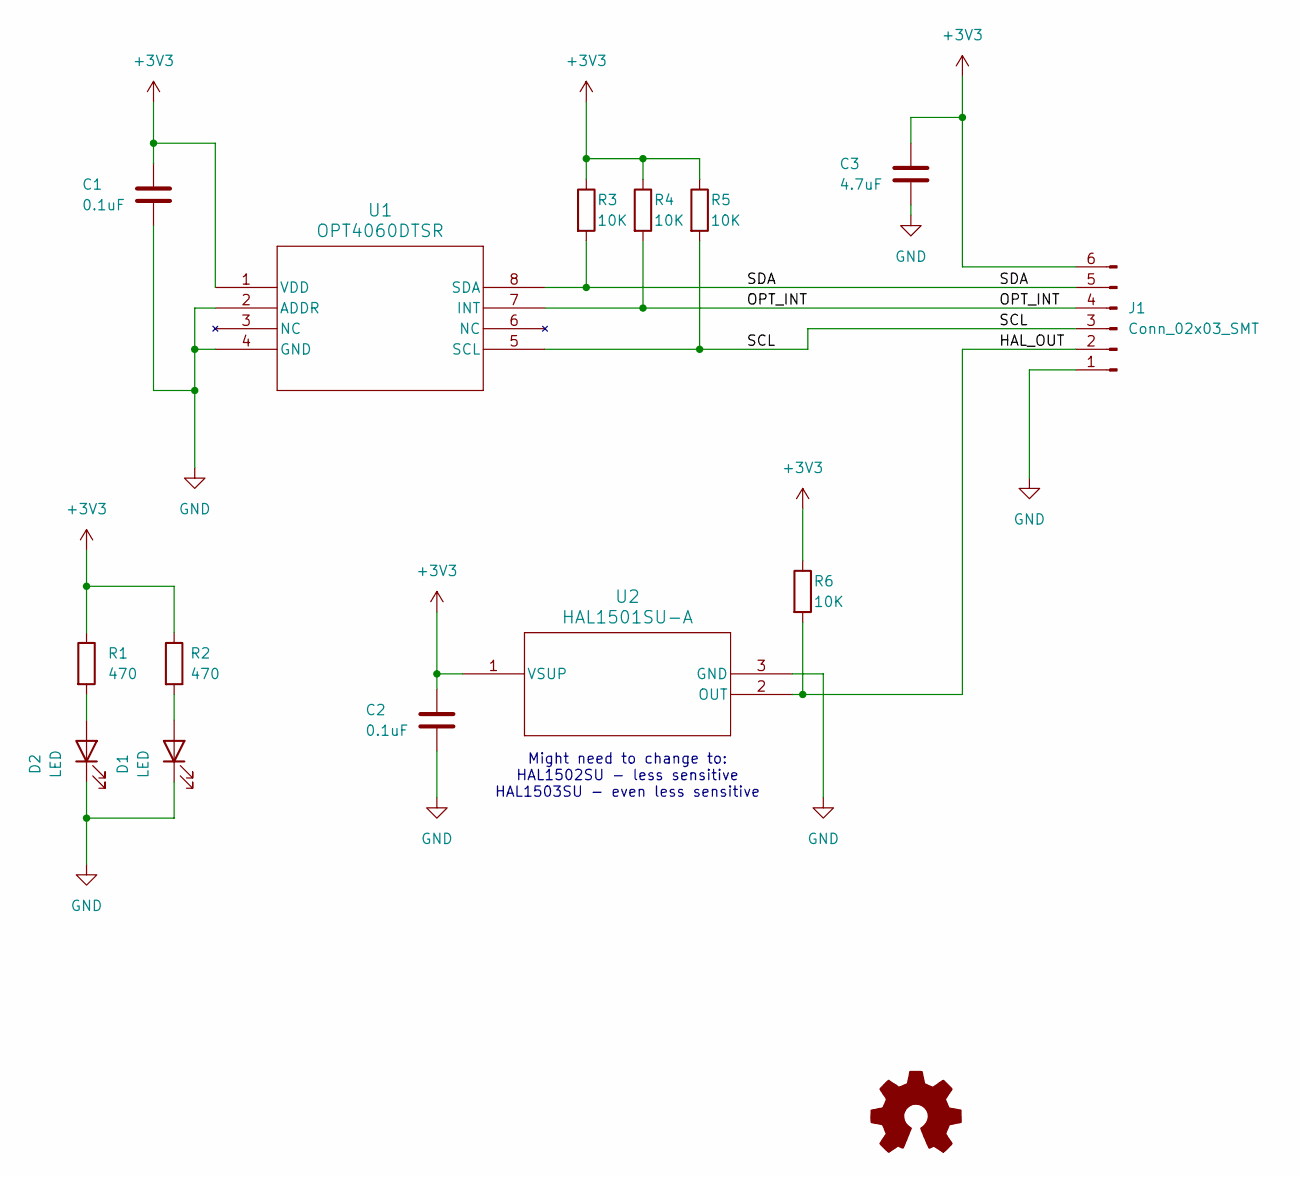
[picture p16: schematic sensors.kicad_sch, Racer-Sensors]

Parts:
C1, C2: 0.1uF; C_0603_1608Metric
C3: 4.7uF; C_0603_1608Metric
D1, D2: LED; LED_0603_1608Metric
J1: Conn_02x03_SMT; PinHeader_2x03_P1.27mm_Vertical_SMD
R1, R2: 470; R_0603_1608Metric
R3, R4, R5, R6: 10K; R_0603_1608Metric
U1: OPT4060DTSR; FCSOT8_DTS_TEX
U2: HAL1501SU-A; SOT-23_TO-236_TDK

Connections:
+3V3: C1.1, C2.1, C3.1, J1.6, R1.1, R2.1, R3.1, R4.1, R5.1, R6.1, U1.1 (VDD), U2.1 (VSUP)
/HAL_OUT: J1.2, R6.2, U2.2 (OUT)
/OPT_INT: J1.4, R4.2, U1.7 (INT)
/SCL: J1.3, R5.2, U1.5 (SCL)
/SDA: J1.5, R3.2, U1.8 (SDA)
GND: C1.2, C2.2, C3.2, D1.1 (K), D2.1 (K), J1.1, U1.2 (ADDR), U1.4 (GND), U2.3 (GND)
unnamed: D1.2 (A), R2.2
unnamed: D2.2 (A), R1.2

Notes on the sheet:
Might need to change to: HAL1502SU - less sensitive HAL1503SU - even less sensitive

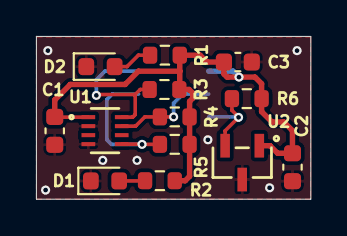
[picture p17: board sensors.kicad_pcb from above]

Board: 4 copper layers, 15.2 x 9.0 mm, 14 parts (1 on the bottom side), 8 nets.

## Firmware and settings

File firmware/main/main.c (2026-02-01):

/**
 * @file main.c
 * @brief Main application entry point for the Racer3 firmware
 * 
 * This file contains the main application logic for the Racer3 autonomous racing car.
 * It initializes all subsystems including BLE, motors, LEDs, color sensors, and battery monitoring.
 * The main loop handles color detection, game state management, and battery monitoring.
 * 
 * @author StuckAtPrototype, LLC
 * @version 1.0
 */

#include <stdio.h>
#include <inttypes.h>
#include "sdkconfig.h"
#include "freertos/FreeRTOS.h"
#include "freertos/task.h"
#include "freertos/queue.h"
#include "freertos/semphr.h"
#include "esp_chip_info.h"
#include "esp_flash.h"
#include "esp_system.h"
#include "esp_log.h"
#include "driver/ledc.h"
#include "driver/gpio.h"
#include "motor.h"
#include <math.h>

// BLE (Bluetooth Low Energy) subsystem
#include "gap.h"
#include "gatt_svr.h"
#include "nvs_flash.h"
#include "esp_bt.h"

// Addressable LED control subsystem
#include "ws2812_control.h"
#include "led_color_lib.h"
#include "led.h"

// Battery monitoring subsystem
#include "battery.h"

// GPIO interrupt handling for color sensor triggers
#include "gpio_interrupt.h"

// I2C configuration for color sensor communication
#include "i2c_config.h"

// Color sensor and prediction subsystems
#include "tcs3400.h"
#include "color_predictor.h"
#include "controller.h"
#include "ring_buffer_rgb.h"



// LEDC (LED Controller) configuration for motor PWM control
#define LEDC_TIMER              LEDC_TIMER_0
#define LEDC_MODE               LEDC_LOW_SPEED_MODE
#define LEDC_DUTY_RES           LEDC_TIMER_10_BIT  // 10-bit duty resolution (0-1023)
#define LEDC_FREQUENCY          (15000)            // 15 kHz PWM frequency

// Motor GPIO pin assignments
#define MOTOR_A_FWD_GPIO        13  // Motor A forward direction pin
#define MOTOR_A_BWD_GPIO        14  // Motor A backward direction pin
#define MOTOR_B_FWD_GPIO        4   // Motor B forward direction pin
#define MOTOR_B_BWD_GPIO        5   // Motor B backward direction pin

// Global variables
static bool motor_direction[NUM_MOTORS] = {true, true};  // Motor direction state (true=forward, false=backward)

QueueHandle_t gpio_intr_evt_queue = NULL;  // Queue for GPIO interrupt events
//NeuralNetwork nn;  // Neural network for color prediction (currently unused)

ring_buffer_t rbg_buffer;  // Ring buffer for RGB color data averaging

// Battery monitoring variables
static bool low_battery_warning = false;      // Low battery warning flag
static uint32_t battery_check_counter = 0;    // Counter for battery check timing

// Function prototypes
void gpio_interrupt_task(void *pvParameters);
void rbg_read(void);

/**
 * @brief Convert RGB color values to hue value
 * 
 * This function converts RGB color values from the OPT4060 color sensor to a hue value
 * in the range 0-65535, which is compatible with the LED color library.
 * 
 * @param red Red component value from color sensor
 * @param green Green component value from color sensor  
 * @param blue Blue component value from color sensor
 * @param clear Clear channel value (unused in this function)
 * @return uint16_t Hue value in range 0-65535
 */
uint16_t opt4060_to_hue(uint16_t red, uint16_t green, uint16_t blue, uint16_t clear) {
    float r_norm, g_norm, b_norm;
    float max, min, hue;

    // Normalize RGB values to the range [0, 1] by dividing by the maximum component
    max = (float)(red > green ? (red > blue ? red : blue) : (green > blue ? green : blue));
    min = (float)(red < green ? (red < blue ? red : blue) : (green < blue ? green : blue));

    r_norm = (float)red / max;
    g_norm = (float)green / max;
    b_norm = (float)blue / max;

    // Calculate hue based on normalized RGB values using standard HSV conversion
    if (max == min) {
        // Grayscale case: Hue is undefined, default to 0
        hue = 0.0f;
    } else if (max == r_norm) {
        hue = 60.0f * ((g_norm - b_norm) / (max - min));
    } else if (max == g_norm) {
        hue = 60.0f * (2.0f + ((b_norm - r_norm) / (max - min)));
    } else { // max == b_norm
        hue = 60.0f * (4.0f + ((r_norm - g_norm) / (max - min)));
    }

    // Ensure hue is positive (handle negative values)
    if (hue < 0.0f) {
        hue += 360.0f;
    }

    // Scale to 0-65535 range as expected by get_color_from_hue function
    return (uint16_t)(hue * 65535.0f / 360.0f);
}


/**
 * @brief Main application entry point
 * 
 * Initializes all subsystems including:
 * - LEDC timer for motor PWM control
 * - LED control system
 * - BLE (Bluetooth Low Energy) communication
 * - Motor control system
 * - Battery monitoring
 * - Color sensor and GPIO interrupt handling
 * 
 * Then enters the main application loop which handles:
 * - Battery voltage monitoring
 * - Color detection and game state management
 * - LED status updates
 */
void app_main(void)
{
    // Configure LEDC timer for motor PWM control
    ledc_timer_config_t ledc_timer = {
            .speed_mode       = LEDC_MODE,
            .timer_num        = LEDC_TIMER,
            .duty_resolution  = LEDC_DUTY_RES,
            .freq_hz          = LEDC_FREQUENCY,
            .clk_cfg          = LEDC_AUTO_CLK
    };
    esp_err_t err = ledc_timer_config(&ledc_timer);
    if (err != ESP_OK) {
        printf("LEDC Timer Config failed: %s\n", esp_err_to_name(err));
        return;
    }

    // Initialize LED control system
    led_init();
    led_set_flash_period(pdMS_TO_TICKS(100));  // Set default flash period to 100ms

    // Initialize BLE (Bluetooth Low Energy) subsystem
    nimble_port_init();
    ble_hs_cfg.sync_cb = sync_cb;
    ble_hs_cfg.reset_cb = reset_cb;
    gatt_svr_init();
    ble_svc_gap_device_name_set(device_name);
    nimble_port_freertos_init(host_task);


    // Configure motor PWM channels for each motor direction
    configure_motor_pwm(MOTOR_A_FWD_GPIO, LEDC_CHANNEL_0);  // Motor A forward
    configure_motor_pwm(MOTOR_A_BWD_GPIO, LEDC_CHANNEL_1);  // Motor A backward
    configure_motor_pwm(MOTOR_B_FWD_GPIO, LEDC_CHANNEL_2);  // Motor B forward
    configure_motor_pwm(MOTOR_B_BWD_GPIO, LEDC_CHANNEL_3);  // Motor B backward

    // Create motor control queues for each motor
    motor_queue[0] = xQueueCreate(MOTOR_QUEUE_SIZE, sizeof(MotorUpdate));
    if (motor_queue[0] == NULL) {
        printf("Failed to create motor queue for Motor A\n");
        return;
    }
    motor_queue[1] = xQueueCreate(MOTOR_QUEUE_SIZE, sizeof(MotorUpdate));
    if (motor_queue[1] == NULL) {
        printf("Failed to create motor queue for Motor B\n");
        return;
    }

    // Create semaphore for synchronizing motor start operations
    motor_start_semaphore = xSemaphoreCreateCounting(4, 0);
    if (motor_start_semaphore == NULL) {
        printf("Failed to create motor start semaphore\n");
        return;
    }

    // Create motor control tasks for each motor
    xTaskCreate(motor_task, "motor_task_A", 2048, (void *)0, 1, NULL);
    xTaskCreate(motor_task, "motor_task_B", 2048, (void *)1, 1, NULL);

    // Initialize the motor controller subsystem
    controller_init();

    // Initialize battery monitoring system
    esp_err_t ret = battery_init();
    if (ret != ESP_OK) {
        ESP_LOGE("main", "Battery initialization failed");
        return;
    }

    // Initialize neural network for color prediction (currently unused)
    //initialize_neural_network(&nn);

    // Initialize ring buffer for RGB color data averaging
    ring_buffer_init(&rbg_buffer);

    // Initialize GPIO interrupt system for color sensor triggers
    configure_gpio_interrupt();
    gpio_intr_evt_queue = gpio_interrupt_get_evt_queue();
    xTaskCreate(gpio_interrupt_task, "gpio_interrupt_task", 2048, NULL, 10, NULL);

    // Initialize TCS3400 color sensor
    TCS3400_init();



    // Main application loop
    while (1) {
        // Battery monitoring: Check voltage every 10 iterations (every 100ms)
        battery_check_counter++;
        if (battery_check_counter >= 10) {
            battery_check_counter = 0;
            
            float voltage;
            esp_err_t ret = battery_read_voltage(&voltage);
            if (ret == ESP_OK) {
                // ESP_LOGI("main", "Battery ADC counts: %d", (int)voltage);
                
                // Check for low battery condition (threshold: 3000 ADC counts)
                if (voltage < 3000) {
                    if (!low_battery_warning) {
                        ESP_LOGW("main", "LOW BATTERY WARNING: %d counts", (int)voltage);
                        low_battery_warning = true;
                    }
                } else {
                    if (low_battery_warning) {
                        ESP_LOGI("main", "Battery voltage recovered: %d counts", (int)voltage);
                        low_battery_warning = false;
                    }
                }
            } else {
                ESP_LOGE("main", "Failed to read battery voltage");
            }
        }
        
        // Update LED indicator based on battery status
        if (low_battery_warning) {
            led_set_indicator_color(LED_COLOR_RED);
            led_set_flash_mode(LED_FLASH_INDICATOR);
            led_set_flash_period(pdMS_TO_TICKS(200));  // Flash every 200ms for low battery
        }
        // When battery is normal, LED control is handled by game state system

        // Read RGB color data from sensor
        rbg_read();

        // Color processing and classification (currently disabled)
        // These commented sections show potential color enhancement techniques:
        // - Gamma correction for brightness adjustment
        // - Saturation enhancement
        // - Color classification and LED control
        
        // Apply gamma correction and increase saturation
        //red_norm = powf(red_norm, 1.8);   // Gamma < 1 brightens
        //green_norm = powf(green_norm, 1.8);
        //blue_norm = powf(blue_norm, 1.8);

        // Re-normalize after gamma correction
        //total = red_norm + green_norm + blue_norm;
        //red_norm = red_norm / total;
        //green_norm = green_norm / total;
        //blue_norm = blue_norm / total;

        // Color classification and LED control
        //process_and_classify_color(red_byte, green_byte, blue_byte, clear);

        // Main loop delay: 10ms (100Hz update rate)
        vTaskDelay(10 / portTICK_PERIOD_MS);
    }
}


/**
 * @brief Read RGB color data from TCS3400 sensor and store in ring buffer
 * 
 * This function reads normalized RGB color values from the TCS3400 color sensor
 * and stores them in the ring buffer for averaging. The sensor returns values
 * normalized to the clear channel for consistent color detection.
 */
void rbg_read(void){
    uint32_t red, green, blue, clear;
    
    // Read normalized color values from TCS3400 sensor
    TCS3400_read_color(&red, &green, &blue, &clear);

    // Color correction factors (currently disabled)
    // These can be used to compensate for sensor characteristics:
    // red *= 2.4;    // Red channel gain
    // green *= 1.0;  // Green channel gain (reference)
    // blue *= 1.3;   // Blue channel gain

    // Color normalization and conversion (currently disabled)
    // This code shows how to convert normalized values to 8-bit RGB:
    // float total = red + green + blue;
    // float red_norm = red / total;
    // float green_norm = green / total;
    // float blue_norm = blue / total;
    // uint8_t red_byte = (uint8_t)(red_norm * 255);
    // uint8_t green_byte = (uint8_t)(green_norm * 255);
    // uint8_t blue_byte = (uint8_t)(blue_norm * 255);

    // Store RGB values in ring buffer for averaging
    ring_buffer_put(&rbg_buffer, red, green, blue);

    // Debug logging (currently disabled)
    // ESP_LOGI("main", "RGB Values: R:%u, G:%u, B:%u, Clear:%lu",
    //     red, green, blue, clear);
}

/**
 * @brief GPIO interrupt task for handling color sensor triggers
 * 
 * This task processes GPIO interrupts from the color sensor and performs
 * color detection and game state management. When an interrupt occurs,
 * it reads multiple color samples, averages them, classifies the color,
 * and updates the game state accordingly.
 * 
 * @param pvParameters Task parameters (unused)
 */
void gpio_interrupt_task(void *pvParameters)
{
    uint32_t io_num;
    for(;;) {
        // Wait for GPIO interrupt event
        if(xQueueReceive(gpio_intr_evt_queue, &io_num, portMAX_DELAY)) {
            ESP_LOGI("main","GPIO[%lu] interrupt occurred!", io_num);

            // Visual feedback for interrupt detection (currently disabled)
            // led_set_taillight_color(LED_COLOR_YELLOW);

            // Small delay to allow sensor to stabilize after interrupt
            // Note: Ideally this should be refactored to avoid delays in interrupt context
            vTaskDelay(pdMS_TO_TICKS(10)); 
            
            // Clear any stale readings by taking an initial sample
            rbg_read();
            
            // Take multiple samples for averaging (4 additional samples)
            for(int i = 0; i < 4; i++){
                vTaskDelay(pdMS_TO_TICKS(3));  // 3ms between samples
                rbg_read();
            }

            uint32_t red, green, blue, clear;
            
            // Alternative sensor reading (currently disabled)
            //opt4060_read_color(&red, &green, &blue, &clear);
            //
            // Neural network color prediction (currently disabled)
            //uint32_t color = predict_color(&nn, red, green, blue, clear);
            //
            // Color correction factors for OPT4060 sensor
            //red *= 2.4;
            //green *= 1.0;
            //blue *= 1.3;
            //
            // Color normalization and conversion
            //float total = red + green + blue;
            //float red_norm = red / total;
            //float green_norm = green / total;
            //float blue_norm = blue / total;
            //uint8_t red_byte = (uint8_t)(red_norm * 255);
            //uint8_t green_byte = (uint8_t)(green_norm * 255);
            //uint8_t blue_byte = (uint8_t)(blue_norm * 255);
            //
            // Note: Color processing should ideally be done outside interrupt context
            // and run at constant intervals, but triggered by interrupt events

            // Get averaged RGB values from ring buffer
            ring_buffer_get_avg(&rbg_buffer, &red, &green, &blue);

            // Classify the detected color
            color_class_t color = classify_color_rgb(red, green, blue, 0);

            ESP_LOGI("main", "Average RGB Values: R:%lu, G:%lu, B:%lu color: %s",
                     red, green, blue, get_color_name(color));

            // Update game state based on detected color
            command_set_game_status(color);

            // Additional LED control (currently disabled)
            //vTaskDelay(pdMS_TO_TICKS(500));
            //led_set_taillight_color(LED_COLOR_RED);
        }
    }
}

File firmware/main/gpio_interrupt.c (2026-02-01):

/**
 * @file gpio_interrupt.c
 * @brief GPIO interrupt handling implementation
 * 
 * This file implements GPIO interrupt handling for the Racer3 device, specifically
 * for triggering color sensor readings. It provides interrupt configuration,
 * debouncing, and event queue management for reliable GPIO event processing.
 * 
 * @author StuckAtPrototype, LLC
 * @version 1.0
 */

#include "gpio_interrupt.h"
#include <stdio.h>
#include "freertos/task.h"
#include "driver/gpio.h"

// GPIO interrupt configuration
#define GPIO_QUEUE_LENGTH 10                    // Maximum number of queued events
#define GPIO_QUEUE_ITEM_SIZE sizeof(uint32_t)   // Size of each queue item
#define DEBOUNCE_TIME_MS 200                    // Debounce time in milliseconds

// Global queue for GPIO events
QueueHandle_t gpio_evt_queue = NULL;

/**
 * @brief Get the GPIO event queue handle
 * 
 * This function returns the handle to the GPIO event queue, allowing other
 * tasks to receive GPIO interrupt events.
 * 
 * @return Handle to the GPIO event queue, or NULL if not initialized
 */
QueueHandle_t gpio_interrupt_get_evt_queue(void){
    return gpio_evt_queue;
}

/**
 * @brief GPIO interrupt service routine
 * 
 * This ISR handles GPIO interrupts with debouncing to prevent spurious
 * triggers. It only processes falling edge interrupts and implements
 * a time-based debounce mechanism.
 * 
 * @param arg GPIO number passed as argument
 */
static void IRAM_ATTR gpio_isr_handler(void* arg)
{
    static uint32_t last_interrupt_time = 0;
    uint32_t interrupt_time = xTaskGetTickCountFromISR();
    uint32_t gpio_num = (uint32_t) arg;

    // Check if it's a falling edge (GPIO level is low)
    if (gpio_get_level(gpio_num) == 0) {
        // Debounce mechanism: only process if enough time has passed
        if (interrupt_time - last_interrupt_time > pdMS_TO_TICKS(DEBOUNCE_TIME_MS)) {
            xQueueSendFromISR(gpio_evt_queue, &gpio_num, NULL);
            last_interrupt_time = interrupt_time;
        }
    }
}

/**
 * @brief Configure GPIO interrupt for color sensor trigger
 * 
 * This function sets up the GPIO interrupt system for triggering color sensor
 * readings. It creates an event queue, configures the interrupt pin, and
 * installs the interrupt service routine with debouncing.
 */
void configure_gpio_interrupt(void)
{
    // Create a queue to handle GPIO events from ISR
    gpio_evt_queue = xQueueCreate(GPIO_QUEUE_LENGTH, GPIO_QUEUE_ITEM_SIZE);

    // Configure the GPIO pin for interrupt
    gpio_config_t io_conf = {};
    io_conf.intr_type = GPIO_INTR_NEGEDGE;              // Interrupt on falling edge only
    io_conf.pin_bit_mask = (1ULL << INTERRUPT_PIN);     // Bit mask of the pin
    io_conf.mode = GPIO_MODE_INPUT;                     // Set as input
    io_conf.pull_up_en = GPIO_PULLUP_ENABLE;            // Enable pull-up resistor
    io_conf.pull_down_en = GPIO_PULLDOWN_DISABLE;       // Disable pull-down resistor
    gpio_config(&io_conf);

    // Install GPIO ISR service
    gpio_install_isr_service(0);

    // Attach the interrupt service routine to the pin
    gpio_isr_handler_add(INTERRUPT_PIN, gpio_isr_handler, (void*) INTERRUPT_PIN);

    printf("GPIO %d configured for interrupt on falling edge only with pull-up enabled and %d ms debounce\n", INTERRUPT_PIN, DEBOUNCE_TIME_MS);
}

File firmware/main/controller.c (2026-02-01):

/**
 * @file controller.c
 * @brief Motor controller and game state management
 * 
 * This file implements the motor controller system that manages motor commands
 * and game state based on color detection. It handles different game modes
 * including speedup, slowdown, and spinout effects.
 * 
 * @author StuckAtPrototype, LLC
 * @version 1.0
 */

#include "controller.h"
#include "motor.h"
#include <stdio.h>
#include "esp_log.h"
#include "led.h"

// Motor control state variables
static MotorCommand current_command;           // Current motor command being processed
static SemaphoreHandle_t command_mutex;        // Mutex for thread-safe command access
static TaskHandle_t controller_task_handle = NULL;  // Handle for controller task
static TimerHandle_t command_timer;            // Timer for motor command duration
static TimerHandle_t command_game_timer;       // Timer for game state duration

// Game state management
game_status state;                             // Current game state (speedup, slowdown, spinout, off)

// Cooldown mechanism to prevent rapid state changes
// Provides immunity period after hitting an obstacle (yellow detection)
static TickType_t cooldown_end = 0;

/**
 * @brief Set game status based on detected color
 * 
 * This function processes color detection results and sets the appropriate game state.
 * Different colors trigger different game effects:
 * - Yellow: Spinout effect (1 second duration with cooldown)
 * - Red/Green: Speed boost effect (10 seconds duration)
 * - Blue: Speed reduction effect (10 seconds duration)
 * 
 * @param detected_color The color detected by the color sensor
 */
void command_set_game_status(color_class_t detected_color){
    uint32_t period = 0;
    TickType_t current_time = xTaskGetTickCount();

    // Process detected color and set appropriate game state
    switch (detected_color) {
        case COLOR_YELLOW: // Spinout effect (obstacle hit)
            // Check cooldown to prevent rapid spinout triggers
            if(current_time < cooldown_end){
                ESP_LOGI("controller", "Yellow cooldown active. Ignoring spinout trigger.");
                return; // Exit early if still in cooldown period
            }
            
            // Stop any active game timer
            if (xTimerIsTimerActive(command_game_timer) == pdTRUE) {
                xTimerStop(command_game_timer, 0);
            }
            
            // Set spinout state and visual feedback
            state = GAME_SPINOUT;
            ESP_LOGI("controller", "YELLOW detected - SPINOUT mode activated");
            led_set_indicator_color(LED_COLOR_YELLOW);
            led_set_flash_mode(LED_FLASH_ALL);  // Flash all LEDs for spinout
            period = 1000; // 1 second spinout duration
            cooldown_end = current_time + pdMS_TO_TICKS(1000); // 1 second cooldown
            break;
            
        case COLOR_RED: // Speed boost effect
        case COLOR_GREEN: // Speed boost effect
            // Stop any active game timer
            if (xTimerIsTimerActive(command_game_timer) == pdTRUE) {
                xTimerStop(command_game_timer, 0);
            }
            
            // Set speed boost state and visual feedback
            state = GAME_SPEEDUP;
            led_set_indicator_color(LED_COLOR_RED);
            period = 10000; // 10 seconds speed boost duration
            ESP_LOGI("controller", "RED/GREEN detected - SPEEDUP mode activated");
            led_set_flash_mode(LED_FLASH_FRONT_ALTERNATE);  // Alternate front LEDs
            break;
            
        case COLOR_BLUE: // Speed reduction effect
            // Stop any active game timer
            if (xTimerIsTimerActive(command_game_timer) == pdTRUE) {
                xTimerStop(command_game_timer, 0);
            }
            
            // Set speed reduction state and visual feedback
            state = GAME_SLOWDOWN;
            led_set_indicator_color(LED_COLOR_BLUE);
            period = 10000; // 10 seconds speed reduction duration
            ESP_LOGI("controller", "BLUE detected - SLOWDOWN mode activated");
            led_set_flash_mode(LED_FLASH_BACK);  // Flash rear LEDs
            break;
            
        default:
            // Unknown color - no game state change
            period = 0;
            break;
    }

    // Start the game timer if a valid game state was set
    if (period != 0) {
        ESP_LOGI("controller", "Starting game timer for %d ms", period);
        xTimerChangePeriod(command_game_timer, pdMS_TO_TICKS(period), 0);
        xTimerStart(command_game_timer, 0);
    }
}

/**
 * @brief Callback function for motor command timer expiration
 * 
 * This function is called when the motor command timer expires, indicating
 * that the current motor command should be stopped. It sends stop commands
 * to both motors.
 * 
 * @param xTimer Timer handle (unused)
 */
void command_timer_callback(TimerHandle_t xTimer)
{
    ESP_LOGI("controller", "Motor command timer expired, stopping motors");

    // Create stop commands for both motors
    MotorUpdate update_a = {0, 0, 0};  // Motor A: speed=0, direction=0
    MotorUpdate update_b = {1, 0, 0};  // Motor B: speed=0, direction=0

    // Send stop commands to motor queues
    BaseType_t xStatus;
    xStatus = xQueueSend(motor_queue[0], &update_a, 0);
    if (xStatus != pdPASS) {
        ESP_LOGE("controller","Failed to send stop command for Motor A");
    }
    xStatus = xQueueSend(motor_queue[1], &update_b, 0);
    if (xStatus != pdPASS) {
        ESP_LOGE("controller","Failed to send stop command for Motor B");
    }
}

/**
 * @brief Callback function for game state timer expiration
 * 
 * This function is called when the game state timer expires, indicating
 * that the current game effect should end. It resets the game state to OFF
 * and restores normal LED behavior.
 * 
 * @param xTimer Timer handle (unused)
 */
void command_game_timer_callback(TimerHandle_t xTimer)
{
    ESP_LOGI("controller", "Game state timer expired, returning to normal mode");
    state = GAME_OFF;
    led_set_indicator_color(LED_COLOR_OFF);
    led_set_flash_mode(LED_CONST);  // Return to constant LED mode
}

// Game effect speed modifiers
#define SPEEDUP_INCREMENT 10      // Speed increase amount for speedup effect
#define SLOWDOWN_DECREMENT 30     // Speed decrease amount for slowdown effect
#define SPINOUT_SPEED 80          // Fixed speed for spinout effect
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

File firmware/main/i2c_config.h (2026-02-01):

/**
 * @file i2c_config.h
 * @brief I2C master configuration header
 * 
 * This header file defines the I2C master configuration for the Racer3 device.
 * It provides centralized I2C settings and initialization functions for
 * communication with various I2C devices such as color sensors.
 * 
 * @author StuckAtPrototype, LLC
 * @version 1.0
 */

#ifndef I2C_CONFIG_H
#define I2C_CONFIG_H

#include "driver/i2c.h"

// I2C master configuration parameters
#define I2C_MASTER_SCL_IO           0                  // GPIO number for I2C master clock (IO0)
#define I2C_MASTER_SDA_IO           1                  // GPIO number for I2C master data (IO1)
#define I2C_MASTER_NUM              0                  // I2C master i2c port number
#define I2C_MASTER_FREQ_HZ          400000             // I2C master clock frequency (400 kHz)
#define I2C_MASTER_TX_BUF_DISABLE   0                  // I2C master doesn't need buffer
#define I2C_MASTER_RX_BUF_DISABLE   0                  // I2C master doesn't need buffer

// I2C function prototypes
/**
 * @brief Initialize I2C master peripheral
 * 
 * This function initializes the I2C master peripheral with the configured
 * parameters including GPIO pins, clock speed, and pull-up settings.
 * It sets up the I2C driver for communication with I2C devices.
 * 
 * @return ESP_OK on success, error code on failure
 */
esp_err_t i2c_master_init(void);

#endif // I2C_CONFIG_H

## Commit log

2024-10-15 version 2.0
    [controller.kicad_pcb, controller.kicad_sch, main-enclosure.step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]
2024-10-18 adding racer v0.2 intial BOM
    [racer-v0.2-BOM.csv]
2024-10-18 added mechanical parts for the racer
    [racer-v0.2-BOM.csv]
2024-10-19 adding the BOM for the sensors PCB
    [sensors-v0.1-BOM.csv]
2024-10-24 hardware: racer.kicad_pcb: Add thickness property to font nodes
    [racer.kicad_pcb]
2024-10-24 hardware: racer.kicad_pcb: Use the correct schematic filename in 'sheetfile' property
    [racer.kicad_pcb]
2024-10-24 hardware: racer.kicad_pcb: Fix wrong value of R22
    [racer.kicad_pcb]
2024-10-24 hardware: racer.kicad_pro: Update project file
2024-10-24 hardware: Add .gitignore file temporary KiCad files
2024-10-24 hardware: sensors.kicad_pcb: Add thickness property to font nodes
    [sensors.kicad_pcb]
2024-10-24 hardware: sensors.kicad_pcb: Fix values of R1 and R2
    [sensors.kicad_pcb]
2024-10-24 hardware: controller.kicad_pcb: Add thickness property to font nodes
    [controller.kicad_pcb]
2025-10-16 removing sdkconfig tracking. we are only supposed to track sdkconfig.defaults
2025-10-17 version 1.0 of CAD files
    [main-enclosure-v1.0.step, main-enclosure.step, top-enclosure-v1.0.step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]
2025-10-17 hardware version 1.0
    [motor_drivers.kicad_sch, racer-v0.2-BOM.csv, racer-v1.0-BOM.csv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]
2025-10-19 reduced gain on the color sensor to 16x to better accomodate variance in LED brightness and tightened the maximum allowed tolerance for color brackets
    [main.c, tcs3400.c]
